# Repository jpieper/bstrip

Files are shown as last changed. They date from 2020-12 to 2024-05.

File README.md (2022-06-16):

# bstrip - High speed automated wire cutter and stripper #

The bstrip is a brushless motor based automated wire processing tool.
It can cut wires to any length, fully strip one side, and pre-cut the
insulation on the back side.  It is based on the mjbots moteus
controller, raspberry pi and mjbots pi3hat, 5208 brushless motors, and
a converted hand v-cut tool.

License: Apache 2.0

This repository contains the bill of materials, models to be printed
on a 3D printer, and python source code for driving the machine.

* [Bill of Materials](BOM.md)
* [Fusion 360 Source CAD](https://a360.co/3fsq1WW)
* [3D printer models](hw/)
* [Source Code](src/cutwire.py)

Overview video: https://www.youtube.com/watch?v=_LFLcuUfIaE

# Build instructions #

TODO

## Raspberry Pi ##

Install a 32 bit Raspberry Pi OS.  A GUI is not required.

Then install the moteus python packages:

```
sudo pip3 install moteus moteus-pi3hat
```

## Setting Motor IDs ##

First, *never* hot plug the power cables, although it is OK to do so
with CAN.

Second, to set the ID for the cutter motor, connect the cutter motor
alone to JC1 on the pi3hat.  Then run:

```
sudo python3 -m moteus.moteus_tool -t 1 --console
conf set id.id 2
<CTRL-D>
sudo python3 -m moteus.moteus_tool -t 2 --console
conf write
<CTRL-D>
```

You should see an `OK` from the `conf write`.  Now both servos can be
daisy chained together on JC1.

## Motor calibration ##

The two motors should then be calibrated, with no load attached:

```
sudo python3 -m moteus.moteus_tool -t 1 --calibrate --cal-invert
sudo python3 -m moteus.moteus_tool -t 2 --calibrate --cal-bw-hz 400
```

## Motor Configuration ##

After setting IDs and calibrating motors, the following configuration files need to be installed on each controller.

```
sudo python3 -m moteus.moteus_tool -t 1 --write-config servo_1.cfg
sudo python3 -m moteus.moteus_tool -t 1 --write-config servo_2.cfg
```

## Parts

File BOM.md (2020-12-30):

# bstrip - Bill of Materials #

The bill of materials looks like this:

* 2x moteus r4.5 controller [mjbots moteus](https://mjbots.com/products/moteus-r4-5)
* 2x mj5208 brushless motor [mjbots mj5208](https://mjbots.com/products/mj5208)
* 1x Raspberry Pi (3 or 4)
* 1x mjbots pi3hat [mjbots pi3hat](https://mjbots.com/products/mjbots-pi3-hat-r4-2)
* 1x Paladin Tools PA1161 Wire Stripper
* 1x MEAN WELL LRS-350-24 24V Power Supply
* 1x URBEST Inlet Fuse Switch Combo [amazon link](https://www.amazon.com/gp/product/B00ME5YAPK)
* 2x 3in x 0.5in EPPDM rubber bands [amazon link](https://amazon.com/gp/product/B07FM7MBGZ)
* rubber feet - [amazon link](https://www.amazon.com/gp/product/B079237LCW)
* Some shoe goo - [amazon link](https://www.amazon.com/gp/product/B01JCCKWZO)

* 3d prints
 * build_plate_1
 * build_plate_2
 * psu_shroud_left
 * psu_shroud_right

* 12x M2.5 heat set inserts - [mcmaster link](https://www.mcmaster.com/94180A321/)
* 29x M3 heat set inserts - [mcmaster link](https://www.mcmaster.com/94180A331/)
  * 4 for left PSU lid
  * 21 for front plate
  * 4 for cross plate
* 3x M4 heat set inserts - [mcmaster link](https://www.mcmaster.com/94180A351/)

* Nx M3x4 low profile hex bolts - [mcmaster link](https://www.mcmaster.com/90666A101/)
* Nx M3x6 low profile hex bolts - [mcmaster link](https://www.mcmaster.com/90666A103/)
* Nx M3x8 low profile hex bolts - [mcmaster link](https://www.mcmaster.com/90666A104/)
* 2x M3 nylon locking nuts - [mcmaster link](https://www.mcmaster.com/90576A102/)
* 4x M4x6 socket head bolts for attaching to PSU and switch - [mcmaster link](https://www.mcmaster.com/91292A107/)
* 2x M4x25 hex head for attaching idler and free wheel - [mcmaster link](https://www.mcmaster.com/91280A144/)
* 2x M4x16 socket head for attaching drive to arm and arm to cutter - [mcmaster link](https://www.mcmaster.com/91292A118/)

* 5x M5 crimp terminals for PSU
* 18 AWG wire for power
* 26 AWG wire for CAN

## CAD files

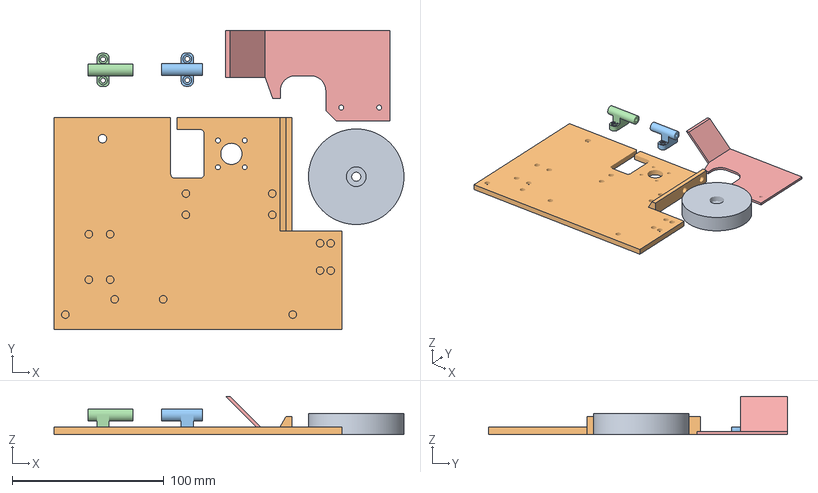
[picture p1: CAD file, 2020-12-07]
hw/build_plate_2.3mf
230.9 x 197.5 x 25.2 mm
free_wheel.stl
body_plate.stl
wire_guide_in.stl
wire_guide_out.stl
output_shield.stl

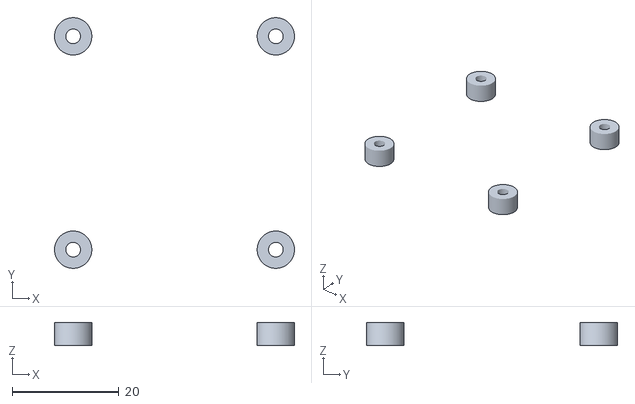
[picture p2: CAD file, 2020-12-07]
hw/stls/drive_controller_spacers.stl
45.0 x 47.0 x 4.40

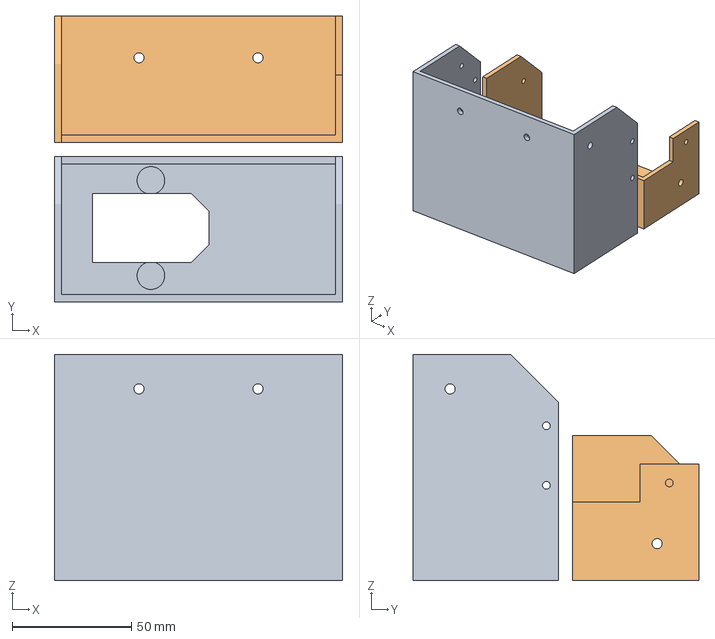
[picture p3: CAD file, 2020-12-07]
hw/psu_shroud.3mf
121.0 x 120.0 x 95.0 mm
psu_shroud_left.stl
psu_shroud_right.stl

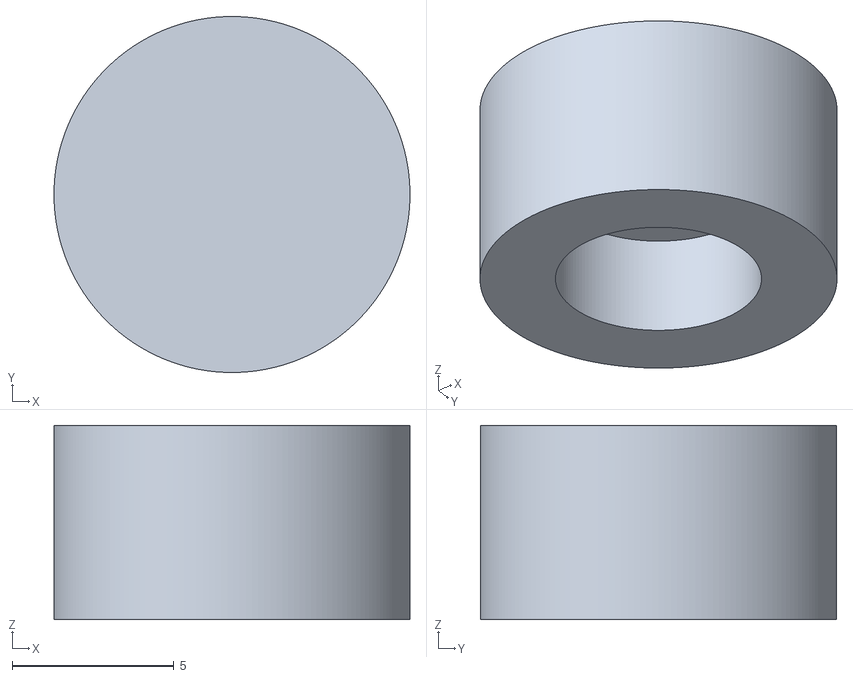
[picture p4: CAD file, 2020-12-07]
hw/stls/magnet_spacer.stl
11.0 x 11.0 x 6.00

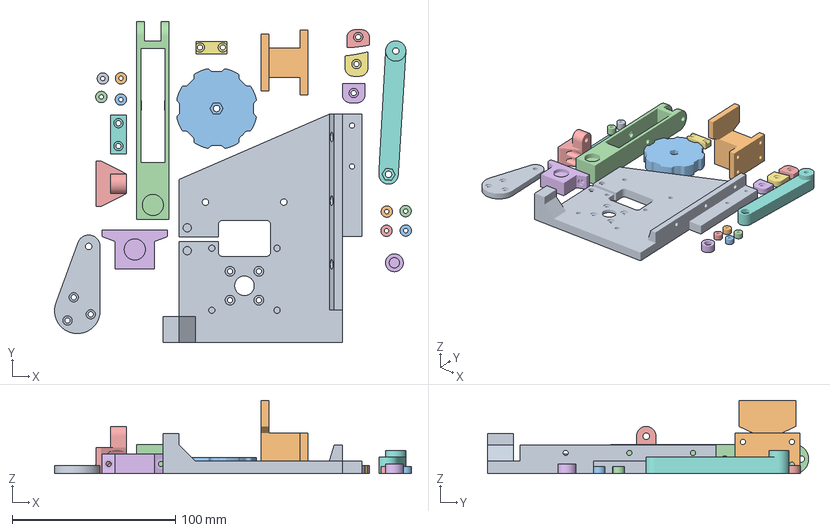
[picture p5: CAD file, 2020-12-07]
hw/build_plate_1.3mf
218.7 x 196.9 x 45.0 mm
cross_plate.stl
idler_capture.stl
spool_holder.stl
idler.stl
idler_bracket.stl
tension_bracket.stl
body_brace.stl
cross_brace.stl
cut_controller_spacers.stl_1
cut_controller_spacers.stl_2
cut_controller_spacers.stl_3
cut_controller_spacers.stl_4
cutter_aligners.stl_1
cutter_aligners.stl_2
cutter_aligners.stl_3
cutter_arm.stl
cutter_drive.stl
drive_controller_spacers.stl_1
drive_controller_spacers.stl_2
drive_controller_spacers.stl_3
drive_controller_spacers.stl_4
magnet_spacer.stl

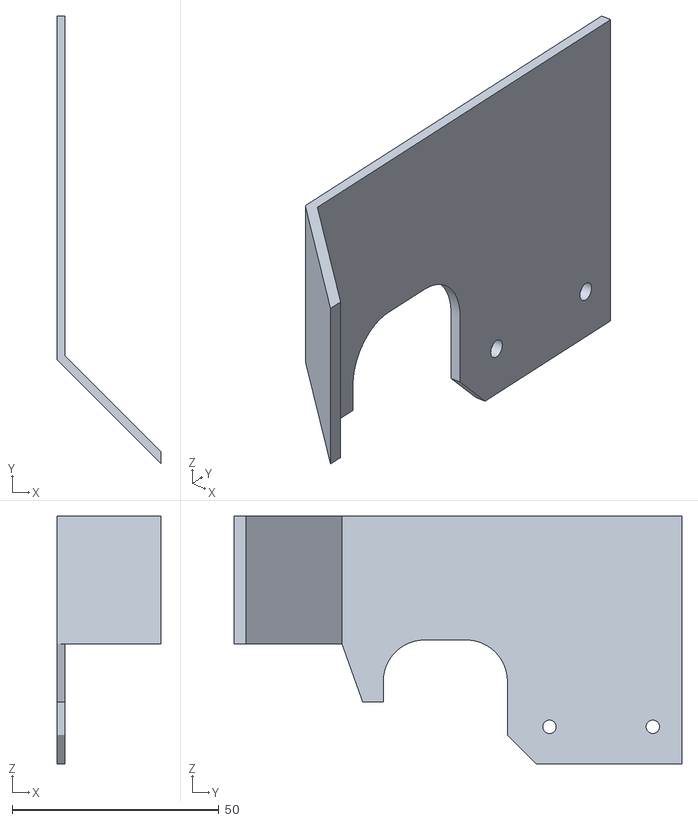
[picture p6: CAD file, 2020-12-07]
hw/stls/output_shield.stl
25.2 x 108.3 x 60.0

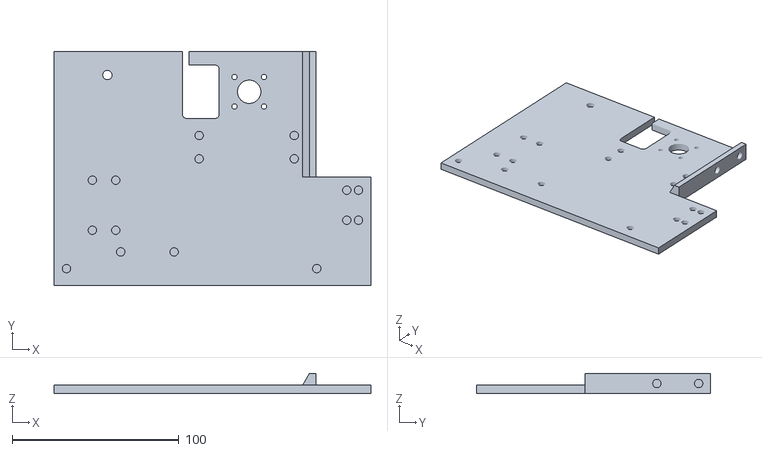
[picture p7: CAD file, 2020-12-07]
hw/stls/body_plate.stl
190.0 x 140.0 x 12.0

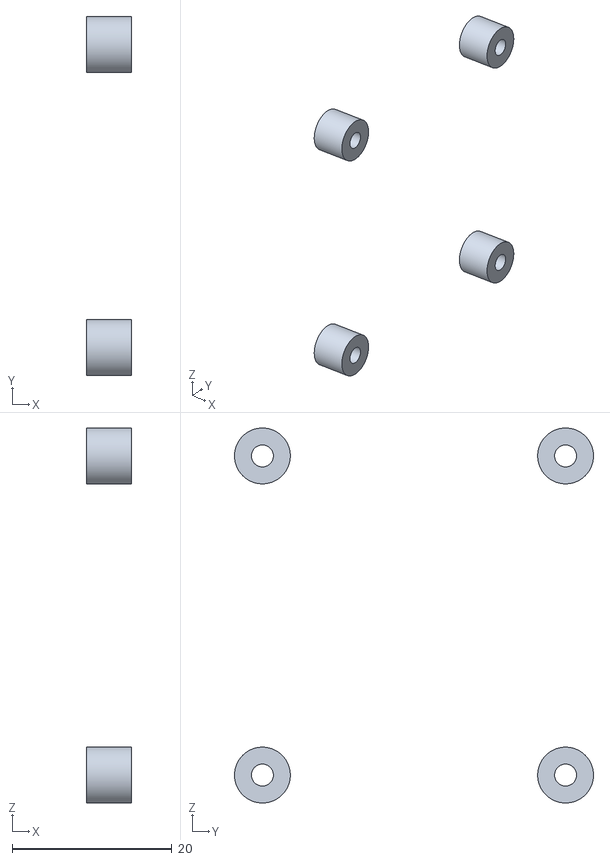
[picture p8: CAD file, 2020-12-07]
hw/stls/cut_controller_spacers.stl
5.65 x 45.0 x 47.0

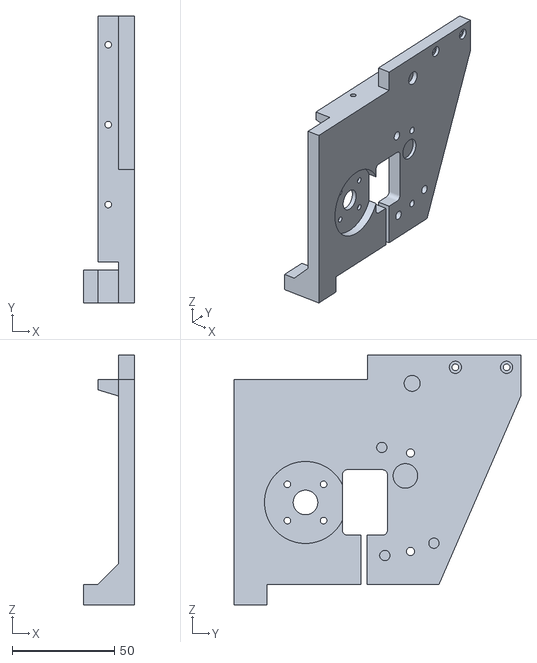
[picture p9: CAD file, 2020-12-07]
hw/stls/cross_plate.stl
24.8 x 140.0 x 122.0

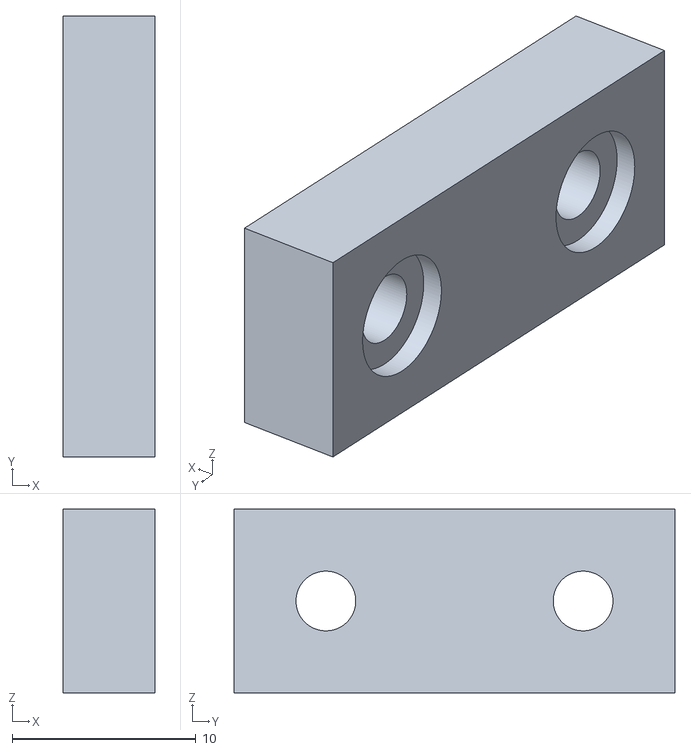
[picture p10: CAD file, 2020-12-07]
hw/stls/cross_brace.stl
5.00 x 24.0 x 10.0

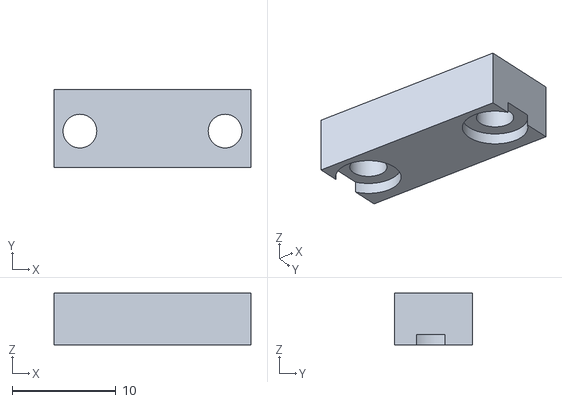
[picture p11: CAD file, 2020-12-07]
hw/stls/body_brace.stl
19.0 x 7.50 x 5.00

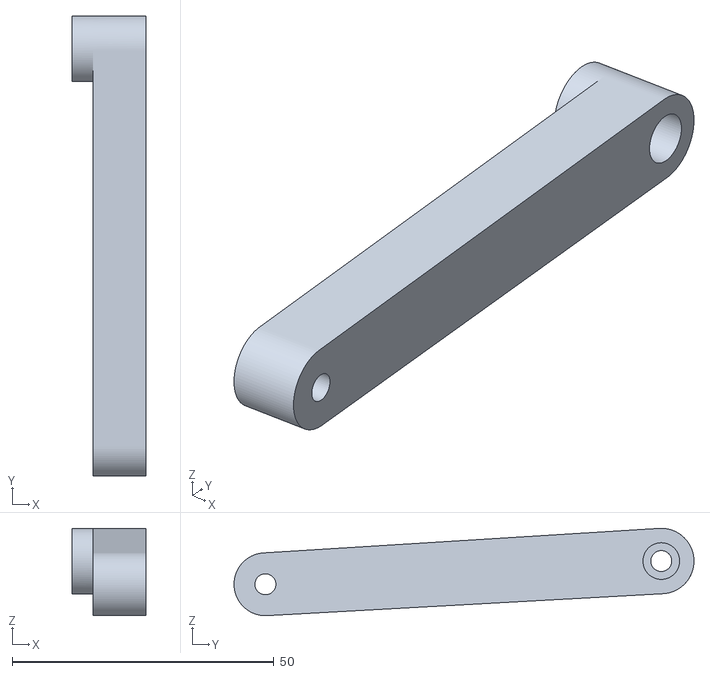
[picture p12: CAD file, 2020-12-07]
hw/stls/cutter_arm.stl
14.2 x 87.8 x 16.7

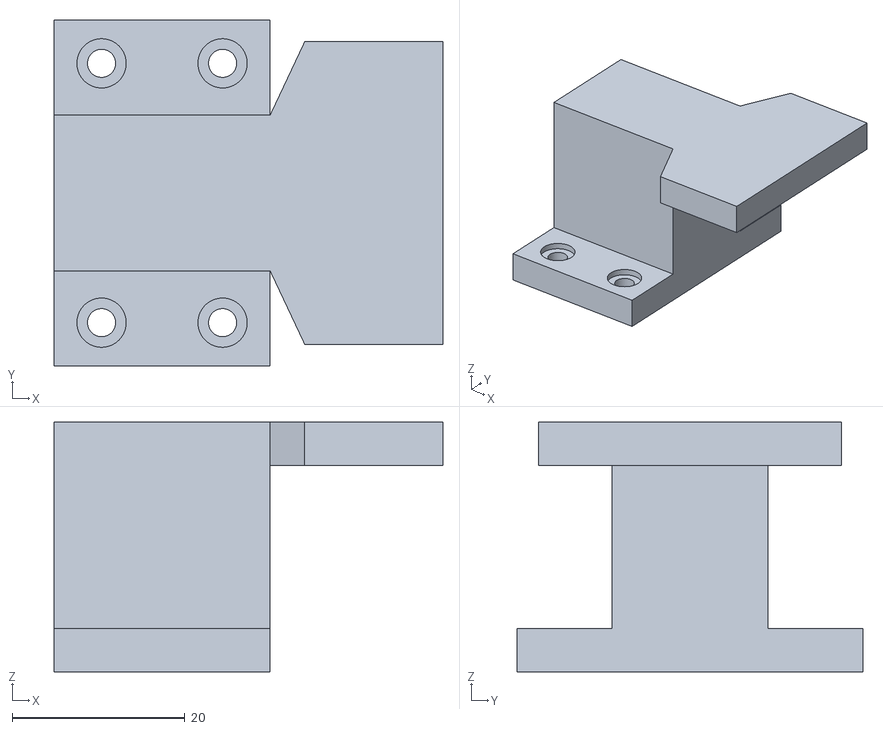
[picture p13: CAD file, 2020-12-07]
hw/stls/idler_capture.stl
45.0 x 40.0 x 28.9

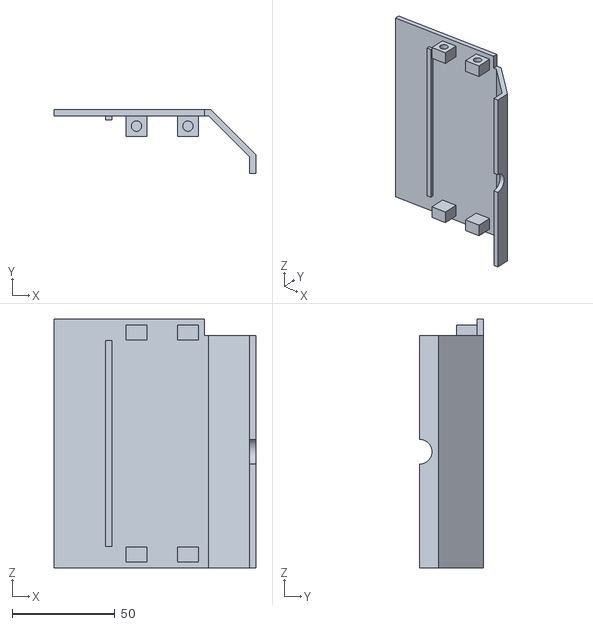
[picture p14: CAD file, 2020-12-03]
hw/stls/shroud_cover.stl
98.0 x 31.0 x 121.0

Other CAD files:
hw/stls/psu_shroud_right.stl
hw/stls/psu_shroud_left.stl
hw/stls/tension_bracket.stl
hw/stls/spool_holder.stl
hw/stls/cutter_aligners.stl
hw/stls/cutter_drive.stl
hw/stls/free_wheel.stl
hw/stls/idler.stl
hw/stls/idler_bracket.stl
hw/stls/wire_guide_in.stl
hw/stls/wire_guide_out.stl

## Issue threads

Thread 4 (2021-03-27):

[FEATURE REQUEST] Captive nuts instead of heatset inserts

darigovresearch, 2021-03-27:
We were wondering if it were possible to adjust the STL files so that they can be replaced with captive nuts instead of heatset inserts. Heatset inserts tend to be more expensive to buy and difficult to correctly insert.

Captive nuts could be the regular hexagonal ones or you can also get square ones depending on the torque requirements. Regular ones would be preferred if possible as they are easy to source.

Is this a possibility as it would greatly simplify the build?

NB: For context for anyone else who is reading this captive nuts are when there is a horizontal slot for a nut to slide in and you then screw your bolt through a designated hole.

jpieper, 2021-03-27:
Heat set inserts have some nice properties: you can print them in more orientations than captive nuts and they also can support significantly more load and torque than a captive nut.

Have you tried inserting heat set inserts?  Once you know the trick they are trivial to do quickly and correctly.  You just need a temperature controlled soldering iron and a small flat piece of metal.  I use a 4cm x 4cm block of 6061.  You use a regular soldering iron tip set to 650F/340C to push it in 95% of the way, and let it set for 2s to heat up the plastic.  Then you press down with the flat block to force the insert in the rest of the way.  That results in it both being flush with the plastic, aligned parallel with the surface, and it flattens out any plastic that would otherwise have formed a mound around the perimeter.

In the scheme of this build, the heat set inserts are less than 1% of the total cost.  In the US at least, you can get the M3 ones from McMaster for $0.13 each https://www.mcmaster.com/94180A331/ .  Given that low relative cost and their benefits, I'm not going to switch to captive nuts.

darigovresearch, 2021-03-28:
Yeah we agree that relative to the total cost of the BOM that in this case the cost is a very small percentage. It was just a thought that came across our mind after watching the [Index PnP build playlist](https://www.youtube.com/playlist?list=PLIeJXmcg1baLBz3x0nCDqkYpKs2IWGHk4) where he had designed some of his 3D printed parts at first to have heatset inserts but then later decided to use captive nuts at a stage when a new revision was due. It was via their channel that we heard about your project.

We're based in the UK and so even though McMaster is a great resource it takes a while to arrive if we need something in a pinch. We have tried heat set inserts but we find it difficult and hard to recover if we make a mistake which results in needing to reprint and start again which can particularly.

No need to redesign it, just wanted to get your thoughts on the idea. You raise a good point about ability carry more load and torque. Was wondering how much load the specific heatsets need in this application. Generally speaking when using heatset inserts also need to take into account in the printing that there are enough outer shell layers and that the infill is not too sparse so it has somewhere to grip on to right?

jpieper, 2021-03-28:
Once I got the above described trick with inserts, I've done well over 2,000 with 0 problems and they all go very quickly.

The .3mf files for bstrip all account for the inserts, but yes, you have to do at least minimal care when designing for them.  Often just using 3 perimeters is enough.

In this application I have no idea how much torque is required, and I'm glad not to have to have spent brain cycles on it!

Best of luck!

Closed 2021-03-28.

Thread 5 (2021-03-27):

[FEATURE REQUEST] Source files for STLs

darigovresearch, 2021-03-27:
Having the source files (depending on the accessibility of the software) would help make iterative updates to the 3D printed STL files would greatly improve the likelihood of someone being able to contribute back to the project. Such as resolving feature request #4 would be easier to tweak the source file than adjusting the STLs or reverse engineering them.

Many open source projects use FreeCAD or OpenSCAD and from experience FreeCAD is easier to use for new joiners to a project.

What did you build this project with and are you able or willing to add them to the repository?

jpieper, 2021-03-27:
This was developed in Fusion 360.  I will post a link to a shareable version of the source in the README.  However, I'm not going to switch it to FreeCAD or OpenSCAD (although of course you're welcome to fork it and do so).  I've done a lot of work in FreeCAD in the past, and I've found that I can get things done about 90% faster in Fusion 360.  Given that when I'm working, I greatly prefer to spend my time designing things instead of futzing with the CAD tool, that's the tradeoff I'm making.

darigovresearch, 2021-03-28:
@jpieper yeah totally agree that it's not worth your time to redo and agree that making is more important that messing with the CAD tools. We're sure the Fusion links will be beneficial to someone so thanks for making it public!

Closed 2021-03-27.

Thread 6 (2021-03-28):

[FEATURE REQUEST] Circuit Diagram/Assembly Instructions

darigovresearch, 2021-03-28:
It would be really helpful for anyone building to follow some assembly instructions or wiring diagram for bstrip.

Do you happen to have any reference assembly instructions or circuit diagrams that you used to build the design?

The exploded view helps but sometimes the order of assembly can make it hard to assemble certain sections towards the end.

jpieper, 2021-03-28:
Nope.  There is really only one way to assemble and wire it up and it should be relatively straightforward.  If you have specific questions, don't hesitate to join the mjbots discord and ask: https://discord.gg/W4hUpBb

Closed 2021-03-28.

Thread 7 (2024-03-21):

Possible use for 13 mm pvc pipe ?

CorentinLemaitre, 2024-03-21:
Hello,

I have found your project on hackaday and it seems really great! 👏👏👏
I was wondering if there is a maximal diameter to use with ?
I would like to cut pvc hose of 13 mm outter diameter and 10 mm inner diameter.

I could make a fork of your project and change the cutting tool to make it work but may be there will be other issue with this design.
As you have designed it, I think you will know if it will be possible to adapt or if it is not possible.

jpieper, 2024-03-21:
Well, anything is possible with enough effort!  You would need a different cutting tool, and likely a different feed mechanism.

CorentinLemaitre, 2024-03-22:
Ok thank you for your feedback, at least there is no big rock on the road.

I will start digging on this direction. I think I will start in one or two month.

Closed 2024-03-22.

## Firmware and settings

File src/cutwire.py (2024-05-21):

#!/usr/bin/python3

# Copyright 2020-2022 Josh Pieper, jjp@pobox.com.
#
# Licensed under the Apache License, Version 2.0 (the "License");
# you may not use this file except in compliance with the License.
# You may obtain a copy of the License at
#
#     http://www.apache.org/licenses/LICENSE-2.0
#
# Unless required by applicable law or agreed to in writing, software
# distributed under the License is distributed on an "AS IS" BASIS,
# WITHOUT WARRANTIES OR CONDITIONS OF ANY KIND, either express or implied.
# See the License for the specific language governing permissions and
# limitations under the License.

import argparse
import asyncio
import math
import moteus
import time

# How much wire is dispensed for one full revolution of the drive
# wheel.
DRIVE_SCALE_CM = 6.5 * math.pi

PRIME_ADVANCE_CM = 1.0
STRIP_EXTRA_RETRACT_CM = 1.0


class Application:
    def __init__(self, args):
        self.args = args

        qr = moteus.QueryResolution()
        qr.trajectory_complete = moteus.INT8
        self.drive = moteus.Controller(id=1, query_resolution=qr)
        self.cut = moteus.Controller(id=2)

    async def stop(self):
        await self.drive.set_stop()
        await self.cut.set_stop()

    async def initialize(self):
        await self.stop()
        await self.set_wire_start()

    async def debug_delay(self):
        if not self.args.slow:
            return
        await asyncio.sleep(0.5)

    async def set_wire_start(self):
        while True:
            await self.drive.set_rezero(0.0, query=True)

            result = None
            while result is None:
                result = await self.drive.query()

            if abs(result.values[moteus.Register.POSITION]) <= 0.5:
                break

        self.wire_start = result.values[moteus.Register.POSITION]

    async def cut_break(self):
        '''Execute a full break with the cutter.  Actuate it all the way, then
        release it all the way.
        '''
        while True:
            result = await self.cut.set_position(
                position=math.nan,
                velocity=2.0,
                maximum_torque=2.0,
                stop_position=0.0,
                feedforward_torque=-1.0,
                query=True)
            if result:
                if result.values[moteus.Register.POSITION] < 0.006:
                    break

        await asyncio.sleep(0.05)

        while True:
            result = await self.cut.set_position(
                position=math.nan,
                velocity=4.0,
                maximum_torque=1.0,
                stop_position=0.12,
                query=True)
            if result and result.values[moteus.Register.POSITION] > 0.11:
                break

        # Now lock this in with no timeout.
        await self.cut.set_position(
            position=math.nan,
            velocity=0.0,
            maximum_torque=1.0,
            watchdog_timeout=math.nan)

    async def cut_strip(self, extra=False):
        '''Engage the cutter to puncture the insulation, but not the wire.
        Leave it there.
        '''

        while True:
            result = await self.cut.set_position(
                position=math.nan,
                velocity=2.0,
                maximum_torque=2.0,
                stop_position=0.008 if not extra else 0.006,
                feedforward_torque=-0.1,
                watchdog_timeout=math.nan,
                query=True)
            if result and result.values[moteus.Register.POSITION] < 0.016:
                break

        # We wait a bit for the insulation to deform.
        await asyncio.sleep(0.1)

        while True:
            result = await self.cut.set_position(
                position=math.nan,
                velocity=4.0,
                maximum_torque=1.0,
                stop_position=0.014,
                feedforward_torque=-0.05,
                watchdog_timeout=math.nan,
                query=True)
            if result and result.values[moteus.Register.POSITION] > 0.008:
                break

        await asyncio.sleep(0.05)

    async def cut_release(self):
        '''Release the cutter into the disengaged position.  Usually from the
        "strip" position.
        '''

        while True:
            result = await self.cut.set_position(
                position=math.nan,
                velocity=4.0,
                maximum_torque=1.0,
                stop_position=0.12,
                watchdog_timeout=math.nan,
                query=True)
            if result and result.values[moteus.Register.POSITION] > 0.11:
                break


    async def drive_rezero(self):
        '''Rezero the drive wheel.  Should be performed from time to time, at
        the start of a cycle is a good time.'''

        pass

    async def drive_advance(self, distance_cm, kp=None, feedforward=None):
        '''Move the drive to the given distance as measured from the "wire
        start".
        '''

        desired_pos = self.wire_start + distance_cm / DRIVE_SCALE_CM

        while True:
            result = await self.drive.set_position(
                position=desired_pos,
                velocity=0.0,
                maximum_torque=2.0,
                velocity_limit=3.0,
                accel_limit=15.0,
                watchdog_timeout=math.nan,
                feedforward_torque=feedforward,
                kp_scale=kp,
                query=True)
            if result is None:
                continue
            error_cm = (result.values[moteus.Register.POSITION] -
                        desired_pos) * DRIVE_SCALE_CM
            if (abs(error_cm) < 0.2 and
                result.values[moteus.Register.TRAJECTORY_COMPLETE]):
                break

        await asyncio.sleep(0.20)

    async def wire(self):
        args = self.args

        if args.prime:
            await self.drive_advance(PRIME_ADVANCE_CM)
            await self.cut_break()

        for n in range(args.count):
            print("CUT NUMBER:", n + 1)
            await self.set_wire_start()

            if args.strip != 0.0:
                await self.drive_advance(args.strip)
                await self.debug_delay()

                await self.cut_strip()
                await self.debug_delay()

                await self.drive_advance(-STRIP_EXTRA_RETRACT_CM, kp=1)
                await self.debug_delay()

                await self.cut_release()
                await self.debug_delay()

            if args.cut != 0.0:
                await self.drive_advance(args.length - args.cut)
                await self.debug_delay()

                await self.cut_strip(extra=True)
                await asyncio.sleep(0.1)

                await self.cut_release()
                await self.debug_delay()

            await self.drive_advance(args.length)
            await self.debug_delay()
            await self.cut_break()


async def main():
    parser = argparse.ArgumentParser(description=__doc__)

    # Things for automated wire production.
    parser.add_argument('-l', '--length', type=float,
                        help='overall length in cm')
    parser.add_argument('-s', '--strip', type=float, default=0.0,
                        help='length of strip (0.0 means no strip)')
    parser.add_argument('-c', '--cut', type=float, default=0.0,
                        help='length of opposite side cut (0.0 means no cut)')
    parser.add_argument('-p', '--prime', action='store_true',
                        help='spool and cut a small amount of wire to begin with')
    parser.add_argument('-n', '--count', type=int, default=1,
                        help='make this many instances')
    parser.add_argument('--slow', action='store_true',
                        help='add debugging delays')

    # Debugging single-action options.
    parser.add_argument('-a', '--action', type=str)

    args = parser.parse_args()

    app = Application(args)

    await app.initialize()

    if args.action:
        if args.action == 'break':
            await app.cut_break()
        elif args.action == 'stop':
            await app.stop()
        elif args.action == 'strip':
            await app.cut_strip()
        elif args.action == 'release':
            await app.cut_release()
        elif args.action.startswith('advance'):
            await app.drive_advance(float(args.action.split('_')[1]))
        elif args.action == 'query':
            print(await app.cut.query())
        else:
            raise RuntimeError(f'Unknown action: {args.action}')
    else:
        await app.wire()

    await app.stop()


if __name__ == '__main__':
    asyncio.run(main())

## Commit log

2020-12-03 Initial import of hardware
    [body_plate.3mf, body_plate.stl, cross_plate.3mf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]
2020-12-07 Add 3d models, readme, and draft of BOM
    [body_brace.stl, body_plate.3mf, body_plate.stl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]
2020-12-07 More detail to BOM
2021-03-27 Reference the source Fusion 360 CAD file
    Resolves #5
2022-02-03 Add PID config for servos
    [servo_1.cfg, servo_2.cfg]
2022-02-03 Make the configs actually work
    [servo_1.cfg, servo_2.cfg]
2022-02-03 More configs
    [servo_1.cfg, servo_2.cfg]
2022-06-16 General update * Take advantage of acceleration limited trajectories for the drive wheel * Include more instruction in the README * Update config settings to work with modern controllers that have to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
    [servo_1.cfg, servo_2.cfg]
